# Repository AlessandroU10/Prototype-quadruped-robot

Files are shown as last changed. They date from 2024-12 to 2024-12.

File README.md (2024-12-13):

# Quadruped Robot Prototype

Este proyecto presenta el diseño de un prototipo de robot cuadrúpedo, enfocándose en el cálculo de torques, análisis cinemáticos y validación experimental.
Cálculo de Torques: Se consideran torques estáticos (fuerzas aplicadas y momentos de inercia) y dinámicos (aceleraciones angulares y fuerzas inerciales).
Cinemática Directa e Inversa: Determinación de la posición y orientación del efector final mediante transformadas homogéneas y cálculo de configuraciones articulares para alcanzar objetivos específicos.
Cinemática Diferencial: Uso del Jacobiano analítico para relacionar velocidades articulares y lineales, identificando singularidades que afectan el sistema.
Validación: Verificación de la cinemática directa con herramientas CAD y simulación.

## Keywords
Diseño Mecánico, Robot cuadrúpedo, Cinemáticadirecta, Cinemática Inversa. 

## Authors
- Alesandro Paredes Zenteno
- Luis Alfredo Villafani Sandoval
- Adrian Urriolagotia Marino

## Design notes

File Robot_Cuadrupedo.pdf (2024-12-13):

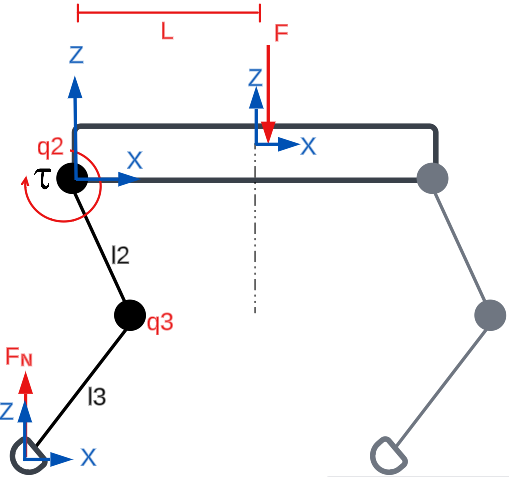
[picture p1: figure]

Departamento de Ingeniería Mecatrónica Robótica (IMT-342) / Número de información 001 @ 2024 Universidad Católica Boliviana "San Pablo" – Unidad Santa Cruz

# Diseño de prototipo de Robot Cuadrúpedo

Resumen: El documento aborda el diseño de un prototipo de robot cuadrúpedo enfatizando aspectos como el cálculo de torques, análisis cinemáticos y verificación experimental. En el dimensionamiento de motores, se analizan tanto el torque estático, basado en fuerzas aplicadas y momentos de inercia, como el torque dinámico, que incorpora aceleraciones angulares y fuerzas inerciales. El análisis de cinemática directa permite determinar la posición y orientación del efector final a través de transformadas homogéneas, mientras que la cinemática inversa calcula las configuraciones articulares necesarias para alcanzar una posición objetivo. La cinemática diferencial, mediante el Jacobiano analítico, relaciona velocidades articulares y lineales, permitiendo detectar singularidades que afectan el rendimiento del sistema. Finalmente, la cinemática directa se verifica empleando herramientas CAD y software de simulación, verificando el modelo planteado.

Palabras clave: Diseño Mecánico, Robot cuadrúpedo, Cinemática directa, Cinemática Inversa.

I.INTRODUCCIÓN
El diseño y desarrollo de robots cuadrúpedos ha capturado la atención de la comunidad científica debido a su capacidad para adaptarse a diversos terrenos y emular características biomecánicas de animales [1]. Entre los desafíos más relevantes para este diseño, se destaca el cálculo de torques para los motores, así como la implementación de análisis cinemático directa, inversa y diferenciales para lograr movimientos de cada extremidad del robot. El objetivo de este proyecto es verificar la cinemática directa e inversa de un prototipo de robot cuadrúpedo mediante simulaciones y pruebas experimentales.

El diseño de torques en robots cuadrúpedos, tanto estáticos como dinámicos, requiere una comprensión detallada de las fuerzas involucradas y de los momentos de inercia de los sistemas rotacionales. Estos cálculos no solo garantizan la estabilidad durante el desplazamiento, sino que también optimizan el consumo energético del robot [2].

Por otra parte, el análisis de la cinemateca directa se centra en determinar la posición y orientación del efector final con base en las variables articulares, mientras que la cinemática inversa busca resolver las configuraciones necesarias de los motores para alcanzar una posición deseada [3]. La cinemática diferencial, por su parte, facilita el análisis de velocidades y fuerzas en tiempo real, siendo una herramienta esencial para controlar la interacción del robot con su entorno

En este contexto, el método de transformadas homogéneas ha demostrado ser eficaz para analizar movimientos de sistemas complejos, como extremidades de robots cuadrúpedos [4]. Además, el uso del Jacobiano analítico permite identificar configuraciones críticas, como puntos de singularidad, que limitan los grados de libertad y afectan el rendimiento general del robot [5].

Por lo tanto, este documento se enfoca en el desarrollo de un prototipo de robot cuadrúpedo que integre estos conceptos, utilizando herramientas de simulación y verificación experimental para garantizar su funcionalidad.

II. DISEÑO DEL ROBOT CUADRÚPEDO

A. Calculo de torque
a) Estatico
El torque estático se calcula en base a la Ec.1.
τest = FL | (1)

Donde:

F | Fuerza aplicada al cuerpo del robot
L | Distancia del centro de masa al eje de rotación

No obstante, debido a la fuerza aplicada (se incluye la masa de una extremidad) en la base del robot, existe una fuerza normal opuesta a la dirección de la fuerza aplicada como se muestra en la Fig.1.

Fig. 1 Diagrama cinemático en vista lateral [Elaboración Propia]

Según la segunda ley de Newton ∑ FZ = ma, se determina la fuerza normal en base a la Ec.2.
FN = F | (2)

Adrian Urriolagotia Marino Dept. Ing. Mecatrónica
Universidad Católica Boliviana Santa Cruz de la Sierra, Bolivia adrian.uriolagotia@ucb.edu.bo

Luis Alfredo Villafani Sandoval Dept. Ing. Mecatrónica
Universidad Católica Boliviana Santa Cruz de la Sierra, Bolivia luis.villafani@ucb.edu.bo

Alesandro Paredes Zenteno
Dept. Ing. Mecatrónica
Universidad Católica Boliviana Santa Cruz de la Sierra, Bolivia alesandro.paredes@ucb.edu.bo

Mgs. José Jesús Cabrera
Dept. Ing. Mecatrónica
Universidad Católica Boliviana Santa Cruz de la Sierra, Bolivia jcabrera@ucb.edu.bo

Departamento de Ingeniería Mecatrónica Robótica (IMT-342) / Número de información 001 @ 2024

Cuando el cuerpo del robot permanece en reposo, la aceleración resulta nula. Esta condición implica que el sistema se encuentra en equilibrio, donde la fuerza normal contrarresta exactamente la fuerza aplicada. En conclusión, la ausencia de aceleración garantiza el balance de fuerzas en el cuerpo.

Considerando lo anterior, en la Tabla 1 se presenta los valores para determinar el torque estático para el motor q2 de una extremidad del robot cuadrúpedo.
TABLA 1 DATOS DE DISEÑO [Elaboración Propia]
N.º | DATOS DEL DISEÑO
Datos | Valor | Unidad
1 | Longitud (L) | 0,07 | m
2 | Masa de carga / 4 | 0,25 | kg
3 | Fuerza (F) | 2,5 | N

De acuerdo a los datos de la Tabla 1, se calcula el torque estático en base a la Ec.1, resultando τest = 0,175 Nm.

b) Dinamico
El torque dinámico corresponde al momento de fuerza necesario para mover un sistema rotacional sujeto a aceleración. Este concepto incluye la resistencia inercial del sistema y las fuerzas externas aplicadas durante el movimiento. La ecuación que describe el torque dinámico se presenta en la Ec.3.
τdin = Imq̈2 + ILq̈2 + τf + τi
(3)

Donde:

Im | Momento de inercia del motor
q̈2 | Aceleración angular
IL | Momento de inercia de la carga
τf | Torque de fricción
τl | Torque de fuerza inercial

En base a la Fig. 1, el motor q2
recibe el mayor torque, debido a que se encuentra a la máxima distancia L desde el eje del motor hasta el centro de masa del robot y conlleva el peso de toda la extremidad para un desplazamiento lineal.

En la Tabla 2 se presentan los datos de diseño.
TABLA 2 DATOS DE DISEÑO [Elaboración Propia]
N.º | DATOS DEL DISEÑO
Datos | Valor | Unidad
1 | Longitud (L) | 0,07 | m
2 | Masa (l2) | 0,015 | kg
3 | Masa (l3) | 0,01 | kg
4 | Masa de carga / 4 | 0,25 | kg
5 | Masa servo motor estimada | 0,015 | kg

La masa total de una extremidad del robot cuadrúpedo se expresa en la Ec.5.
mt = ml2 + ml3 + mq2 + mL
mt = 0.3[Kg] | (5)

El momento de inercia de la carga se presenta en la Ec.6.

IL =

1
3

mLL

2 | (6)

En base a la Ec.6, el momento de inercia de la carga resulta IL = 5x10⁻⁴

[kgm²
].

Según [6], el momento de inercia de un servo motor DC, está dado por Ec.7.
Im = 1,4x10⁻⁶

[Kgm²
] | (7)

Se considera un torque de fricción τf para el cálculo de torque dinámico del motor, según [6], el torque de fricción τf se representa como la Ec.8.
τf = Bmq̇2

(8)

Donde:

τf | Torque de fricción
Bm | Constante de fricción viscosa
q̇2 | Velocidad angula del motor

Para calcular Bm se utiliza la ecuación de la constante de tiempo mecánica del sistema dada por la Ec.9.

Bm =

Im
tm

−

kbkm
Rm

(9)

Donde:

Im | Momento de inercia del motor
tm | Constante de tiempo mecánica
kb, km | Constantes de fuerza electromotriz y de torque
Rm | Resistencia del motor

Según [6], las características del fabricante de un motor DC se presentan en la Tabla 3.

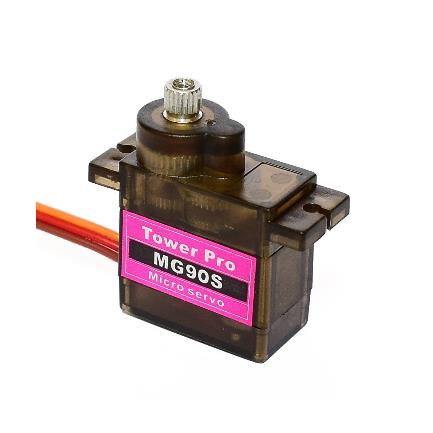
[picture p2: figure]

Departamento de Ingeniería Mecatrónica Robótica (IMT-342) / Número de información 001 @ 2024

TABLA 3 CARACTERISTICAS DEL MOTOR [6]

Nº | MOTOR DC
PARAMETRO | VALOR | UNIDADES

1

2

3

4

5

Dado los valores en la Tabla 6, la constante de fricción viscosa en base a la Ec.9, resulta Bm = 2,012x10⁻⁶Nms.

Los requerimientos del motor se presentan en la Tabla 4.

TABLA 4 REQUERIMIENTOS DEL MOTOR [Elaboración Propia]

Nº | REQUERIMIENTOS DEL MOTOR
REQUERIMIENTO | VALOR | UNIDAD
1 | | 1,4x10⁻⁶ | Kgm²
2 | | 5x10⁻⁴ | Kgm²
3 | q̇2
4 | q̈2

Considerando el requerimiento de q̇2 de la Tabla 4, se calcula el torque de fricción en base a la Ec.8, resultando τf = 1,6x10⁻⁵Nm

La aceleración lineal se considera en el cálculo de torque dinámico debido a que la masa de la extremidad experimenta un movimiento lineal relacionado con la rotación. Esto ocurre porque una aceleración lineal en una masa genera fuerzas inerciales que contribuyen al torque dinámico.

La aceleración lineal se presenta en la Ec.10. dando como resultado: a = 0,35 m
s

2
a = q̈2L | (10)

La ecuación de la fuerza inercial en el centro de masa se presenta en la Ec.11, resultando Finer = 8,75x10⁻³N

Finer = mpataa | (11)

El torque inercial debido a esta fuerza se presenta en la Ec.12, dando como resultado τiner = 6,125x10⁻⁴Nm

τiner = FinerL | (12)

En base a la Ec.3, se obtiene el cálculo del torque dinámico para el motor q2

, que corresponde a: τdin = 3,14x10⁻³Nm.

B. Dimensionamiento de motor
El torque máximo del motor q2
se presenta en la Ec.13,
dando como resultado τmax = 0,18 Nm.
τmax = τesta + τdin | (13)

Según este valor de referencia se dimensiona el servo motor a implementar para una entremediad del robot cuadrúpedo.

Fig. 2 Servo motor MG90S [7]

El servomotor MG90S, mostrado en la Fig. 2, cumple con el torque requerido para el prototipo del robot cuadrúpedo. Las especificaciones técnicas de este servomotor se encuentran detalladas en la Tabla 5. Por lo tanto, este modelo resulta adecuado para las necesidades del proyecto.

TABLA 5 ESPECIFICACIONES DEL MOTOR [7]

Nº | REQUERIMIENTOS DEL MOTOR
REQUERIMIENTO | VALOR | UNIDAD
1 | Voltaje de operación | 3 – 7,2 | VDC
2 | Torque | 0,2 | Nm
3 | Velocidad | 0,1 / 60 | seg grados ⁄
4 | Ancho de pulso | 600 y 240 | μs
5 | Engranajes | Metal
6 | Dimensiones | 22 x 11,5 x 27 | mm
7 | Peso | 13,4 | g

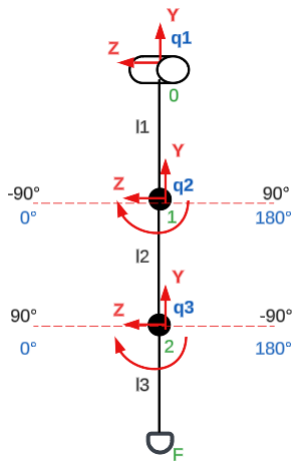
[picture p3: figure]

Departamento de Ingeniería Mecatrónica Robótica (IMT-342) / Número de información 001 @ 2024

C. Selección de componentes
La Tabla 6 se presentan los componentes a utilizar para el desarrollo del robot cuadrúpedo.
TABLA 6 SELECCIÓN DE COMPONENTES [Elaboración Propia]
Nº | Selección de Componentes
Categoría | Componente/ Pieza | Cantidad
1 | Componentes | Arduino uno | 1
2 | | Servo motor MG90S | 6
3 | Elementos Impresos/Externos | Corona | 6
4 | | Base | 1
5 | | Fémur | 2
6 | | Tibia | 2
7 | | Pata de goma | 2
8 | | Pieza 1 izquierda | 1
9 | | Pieza 2 izquierda | 1
10 | | Pieza 1 derecha | 1

Soportes para
Motor
11 | Pieza 2 derecha | 1
III. | ANÁLISIS CINEMÁTICO
A. Cinematica Directa
En la Fig.3 se presenta el diagrama cinemático de una extremidad del robot cuadrúpedo. Se observa que los motores q2 y q3 giran físicamente de 0º a 180º en sentido horario, sin embargo, en la cinemática directa los ángulos se establecen de 90º a -90º grados sentido antihorario siendo 0º en una posición vertical.

Fig. 3 Diagrama cinemático [Elaboracion propia]

Se utiliza el método de transformadas homogéneas para determinar la posición y orientación del punto final, de ese modo obtener la cinemática directa de una extremidad. El análisis se realiza en base a la Fig.3 en un plano Y-Z donde se obtiene las transformada de TI0

, T01, T12 y T2F.

Para simplificar la expresión matemática se considera la notación presentada en la Ec.14 a la Ec.19.

C23 = cos (q

2

− q
3

)
(14)

S23 = sin (q

2

− q
3

)
(15)

C1 = cos(q1)

(16)

S1 = sin(q1)

(17)

C2 = cos(q2)

(18)

S2 = sin(q2)

(19)

En la Ec.20 se presenta la transformada homogénea desde el sistema de coordenadas inercial I al punto 0 donde solo existe una rotación en Z.
TI0 = [
C1 | −S1 | 0
S1 | C1 | 0
0
0 | 0
| 0 | 1
| | 0

0
0

0/1]

(20)

En la Ec.21 se presenta la trasformada homogénea de 0 a 1, donde existe translación en Y y rotación en X.
T01 = [
1 | 0 | 0
0 C2 | −S2
0
0 | S2
| 0 | S2
| | 0

a
−l1
b
1

]

(21)

En la Ec.22 se presenta la trasformada homogénea de 1 a 2, donde existe traslación en Y y rotación en X.
T12 = [
1 | 0 | 0
0 C3 | −S3
0
0 | S3
| 0 | S3
| | 0

c
−l2

0/1]

(22)

Finalmente, en la Ec.23 se presenta la trasformada homogénea de 2 a F, donde solo existe una traslación en Y.

T2F = [

1 0 0
0 1 0
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
(23)

En la Tabla 7 se presenta el valor de las translaciones y desfases que contiene una extremidad.

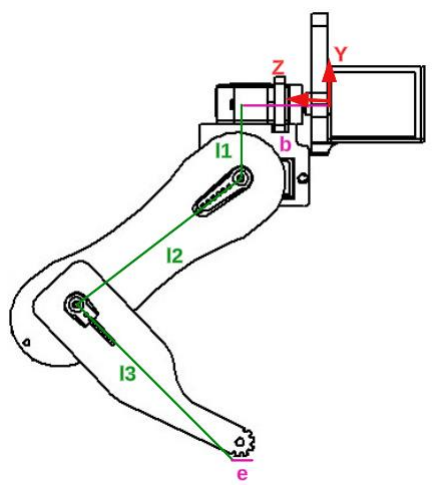
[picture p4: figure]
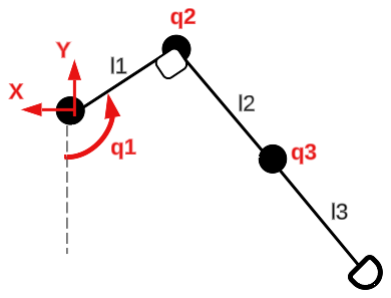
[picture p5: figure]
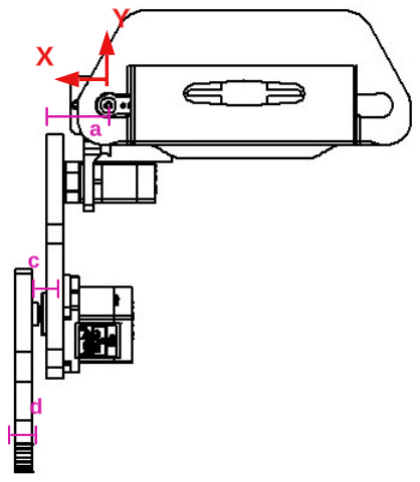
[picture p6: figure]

Departamento de Ingeniería Mecatrónica Robótica (IMT-342) / Número de información 001 @ 2024

TABLA 7 VALOR DE TRANSLACIONES Y DESFASES [Elaboración Propia]

Nº | DATOS DE DIAGRAMA CINEMÁTICO
LONGITUD | VALOR | UNIDAD
1 | a | 17,66 | mm
2 | b | 24,25 | mm
3 | c | 6,9 | mm
4 | d | 0,5 | mm
5 | e | 7,96 | mm
6 | l1 | 22,93 | mm
7 | l2 | 64,49 | mm
8 | l3 | 70,54 | mm

En la Fig.4 y Fig. 5 se observa la ubicación de dichas variables las cuales representan el desfaz que existe entre cada motor y eslabón de una extremidad.

Fig.4 Plano Y-Z de una extremidad [Elaboracion propia]

Fig.5 Plano Y-X de una extremidad [Elaboracion propia]

La transformada homogénea desde el sistema de coordenadas inercial I hasta el punto final F se define como el producto de todas las transformadas intermedias como se presenta el Ec.24.

TIF = TI0T01T12T2F

(24)

De la Ec.24 se obtiene la matriz presentada en la Ec.25 donde se muestra la orientación y posición del punto final.

TIF = [

C1 | −S1C23 | S1S23
S1 | C1C23 | −S23C1
0
0 | S23
| 0 | C23
| | 0

PX
PY
PZ
1

]
(25)

Donde:
Px = aC1 + cC1 + dC1 + eS1S23 + l1S1 + l2S1C2 + l3S1C23 Py = aS1 + cS1 + dS1 − eS23C1 − l1C1 − l2C1C2 − l3C1C23

Pz = b + eC23 − l2S2 − l3S23

La transformada homogénea para las articulaciones restantes presenta una estructura equivalente debido a la similitud en su naturaleza. En conclusión, dicha uniformidad simplifica el análisis y generaliza el procedimiento aplicado.

B. Cinematica Inversa
Mediante el método cerrado, se determina la cinemateca inversa para los motores q1

, q2

, q3
. La Fig.6 presenta el
diagrama cinemático para q1 donde se obtiene la Ec.26. en base a [9].

q1 = tan⁻¹ (

x − c − d
y + l1

) + cos⁻¹ (
a
√(x − c − d)
2 + (y + l1)

2

) (26)

Fig.6 Diagrama cinemático en el plano Y-X [Elaboracion propia]

En la Fig.7 se presenta el diagrama cinemático en el plano Y-Z para q2 y q3 donde se obtiene geométricamente la Ec.27 y Ec.28.

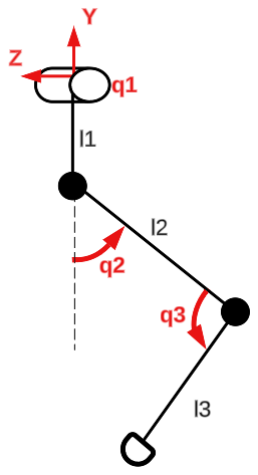
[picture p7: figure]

Departamento de Ingeniería Mecatrónica Robótica (IMT-342) / Número de información 001 @ 2024

Fig.7 Diagrama cinemático en el plano Y-Z [Elaboracion propia]

q2 =

π
2

+ sin⁻¹ (

z + b
√L − a
2

) − cos⁻¹ (
b

2 − a

2 − c

2
2b√L − a
2

) (27)

q3 = cos⁻¹ (
a

2 + b

2 + c

2 − L
2bc | ) | (28)

Donde:
L = (x − c − d)

2 + (z − b)

2 + (y + l1
)

2

C. Cinematica Diferencial
a) Jacobiano Analítico
El Jacobiano Analítico relaciona las velocidades de los motores q̇1

, q̇2 y q̇3 con la velocidad lineal del efector final y viene dada por la Ec.29.

V = J ∗ q̇

(29)

Se determina las derivadas parciales de Px, Py, Pz respecto a
cada articulación q1

, q2

, q3 en base a la Ec.30.

TBF =

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
∂q3 ]

(30)

Donde:

Respecto a q1

∂x
∂q1

= −aS1 − cS1 − dS1 + eS23C1 + l1C1 + l2C1C2 + l3C1C23

∂y
∂q1

= aC1 + cC1 + dC1 + eS1S23 + l1S1 + l2S1C2 + l3S1C23

∂z
∂q1

= 0

Respecto a q2
:
∂x
∂q2

= (eC23 − l2S2 − l3S23)S1

∂y
∂q2

= (−eC23 + l2S2 + l3S23)C1

∂z
∂q2

= −eS23 − l2C2 − l3C23

Respecto a q3
:
∂x
∂q3

= (−eC23 + l3S23)S1

∂y
∂q3

= (eC23 − l3S23)C1

∂z
∂q3

= eS23 + l3C23

b) Singularidad
La singularidad se establece mediante la determinante de la Jacobiano, esta condición indica configuraciones específicas donde la extremidad pierde grados de libertad, afectando su capacidad de movimiento en ciertas direcciones.

El determinante de la matriz Jacobiana se presenta en la Ec.31.

det(JA

) = l2(e

2S23C3 + el1C3 + el2C2C3 + el3S3S23 + el3C3C23 + l1l3S3 + l2l3S3C2 + l3

2
S3C23)

(31)

Se | identificaron | condiciones | que | conducen | a
configuraciones singulares las cuales son:
q2 = q3 = 0°
q2 = 90°, q3 = 0°
q2 = −90°, q3 = 0°

IV. ESPACIO DE TRABAJO
a) Simualcion
En laFig.8 se presenta la simulación del espacio de trabajo de una extremidad simulado en Matlab en base a la cinemateca directa utilizando los rangos de trabajo de la Tabla 8.

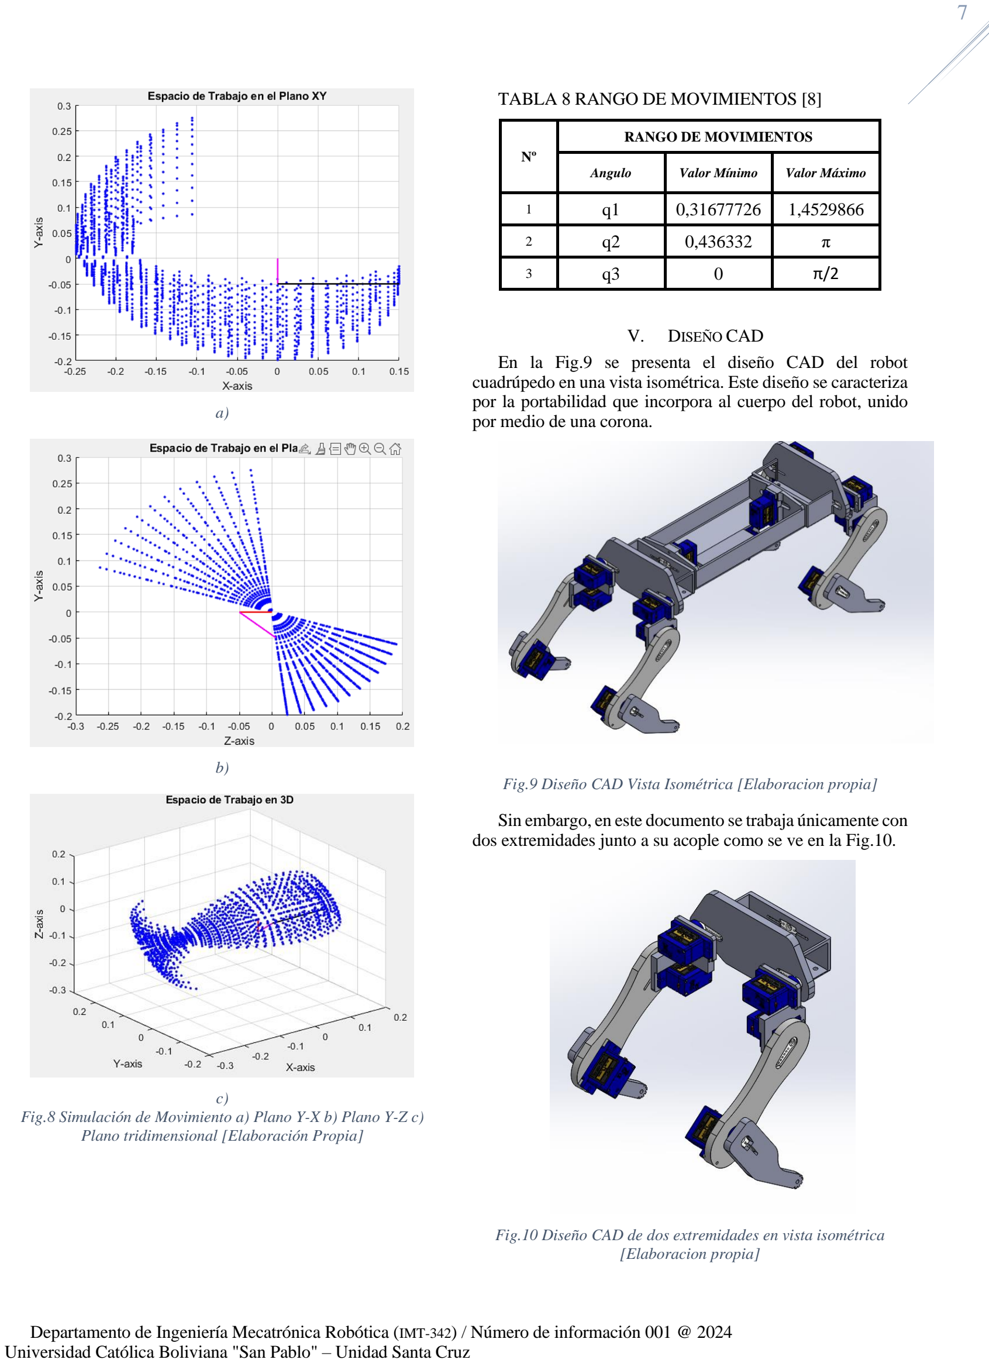
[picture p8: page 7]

Departamento de Ingeniería Mecatrónica Robótica (IMT-342) / Número de información 001 @ 2024

a)

b)

c)
Fig.8 Simulación de Movimiento a) Plano Y-X b) Plano Y-Z c) Plano tridimensional [Elaboración Propia]

TABLA 8 RANGO DE MOVIMIENTOS [8]

Nº | RANGO DE MOVIMIENTOS
Angulo | Valor Mínimo | Valor Máximo
1 | q1 | 0,31677726 | 1,4529866
2 | q2 | 0,436332 | π
3 | q3 | 0 | π/2
V. DISEÑO CAD
En la Fig.9 se presenta el diseño CAD del robot cuadrúpedo en una vista isométrica. Este diseño se caracteriza por la portabilidad que incorpora al cuerpo del robot, unido por medio de una corona.

Fig.9 Diseño CAD Vista Isométrica [Elaboracion propia]

Sin embargo, en este documento se trabaja únicamente con dos extremidades junto a su acople como se ve en la Fig.10.

Fig.10 Diseño CAD de dos extremidades en vista isométrica [Elaboracion propia]

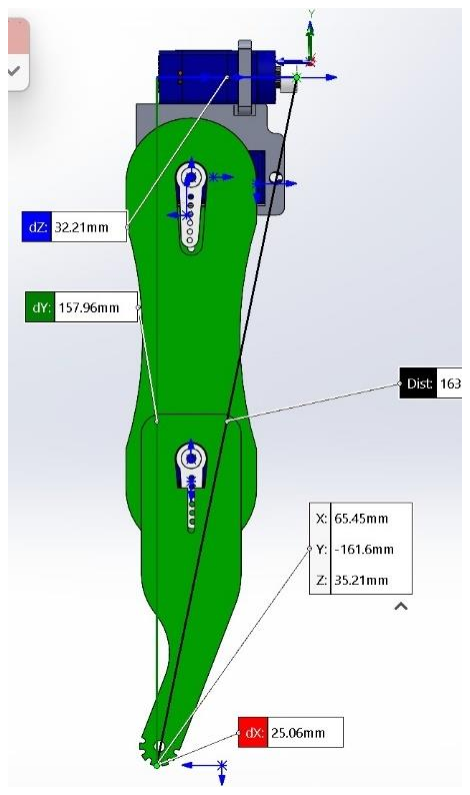
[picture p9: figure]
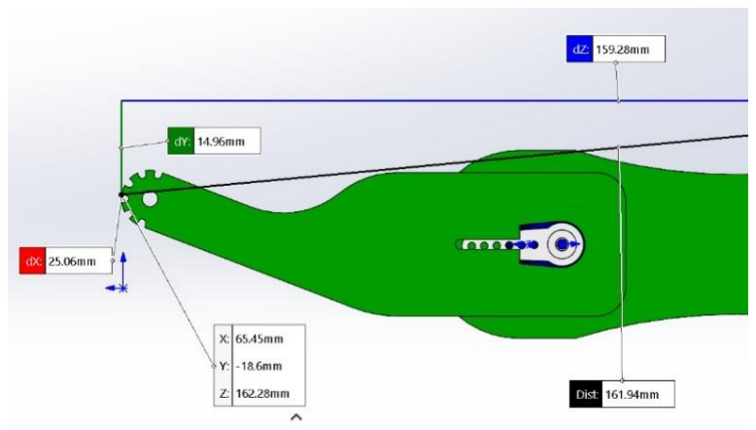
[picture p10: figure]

Departamento de Ingeniería Mecatrónica Robótica (IMT-342) / Número de información 001 @ 2024

VI. VERIFICACIÓN

A. Comprobacion de cinematica directa
Para la comprobación de la cinemática directa se calcula la posición del efector final mediante software VS CODE y se comprueba dicha posición en el software de diseño CAD SOLIDWORKS.

Se presentan tres casos de estudio en cuanto a las posiciones de q2 y q3

siendo q1 = 0°, las cuales se presentan en la Tabla 9.

TABLA 9 CASOS DE ESTUDIO [Elaboración Propia]

Caso | RANGO DE MOVIMIENTOS EN GRADOS °
Motor | Valor
1 | q2 | 0°
| q3 | 0°
2 | q2 | -90°
| q3 | 0°
3 | q2 | 90°
| q3 | 90°
a) Caso 1
Para el caso 1 se presenta la extremidad con un ángulo de q2 = q3 = 0°, resultando la posición final en:

X = [
Px
Py
Pz

] = [
25,06
−157,96

32,21 ]

En la Fig.10 se presenta la extremidad modelada en CAD, donde se determina la distancia en los ejes desde el sistema de coordenadas inercial hasta el punto final. Las mediciones realizadas en x, y, z coinciden con los valores obtenidos en Px, Py, Pz
. Este resultado verifica la comprobación de la cinemateca directa.

Fig. 10 Extremidad con q2

= q3

= 0° [Elaboracion propia]

b) Caso 2
Se comprueba la cinemática directa para q2 = −90° y q3 = 0° , resultando la posición final en:

X = [
Px
Py
Pz

] = [
25,06
−14,97

159,28]

En la Fig.11 se presenta la extremosidad en cuyos ángulos establecidos, donde se observa que las dimensiones en x, y, z corresponden a Px, Py, Pz
(Se recorto la Fig.11 por tema de visualización).

Fig.11 Extremidad con q2

= −90° y q3

= 0°[Elaboracion
propia]

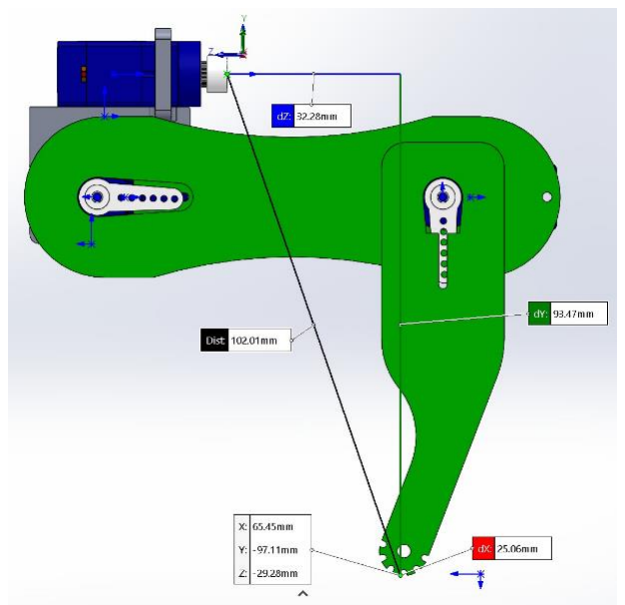
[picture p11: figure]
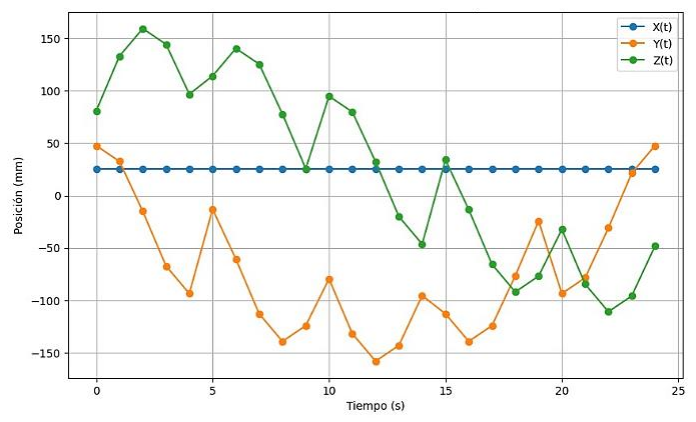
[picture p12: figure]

Departamento de Ingeniería Mecatrónica Robótica (IMT-342) / Número de información 001 @ 2024

c) Caso 3
Se presenta la Fig. 12 para q2 = 90° y q3 = 90° , resultado la cinemateca directa en:
X = [
Px
Py
Pz

] = [
25,06
−93,47

−32,28]

Fig.12 Extremidad con q2

= q3

= 90° [Elaboracion propia]

En la Fig.12 se observa que las dimensiones en x, y, z, corresponden a Px, Py, Pz

La cinemática directa de una extremidad se planteó correctamente, como se verifico al comparar Px, Py, Pz con x, y, z, obtenidas del diseño CAD en los tres casos de estudio.

VII. SIMULACIÓN
Se realiza la simulación en tiempo real de la cinemática directa en Matlab con los siguientes ángulos (q1
, q2

, q3

)
presentados en la Tabla 10.

TABLA 10 RANGO DE MOVIMIENTOS [Elaboración Propia]

Nº | RANGO DE MOVIMIENTO EN GRADOS °
q1 | q2 | q3
1 | 0 | -90 | 90
2 | 0 | -90 | 45
3 | 0 | -90 | 0
4 | 0 | -90 | 45
5 | 0 | -90 | 90
6 | 0 | -45 | 90
7 | 0 | 0 | 90
8 | 0 | 0 | 45
9 | 0 | 0 | 0
10 | 0 | 0 | -45
11 | 0 | 0 | -90
12 | 0 | 45 | -45
13 | 0 | 90 | 0
14 | 0 | 90 | 45
15 | 0 | 90 | 90
16 | 0 | 90 | 45
17 | 0 | 90 | 0
18 | 0 | 90 | 45
19 | 0 | 90 | -90

La Fig.13 presenta el comportamiento de las posiciones x, y, z del punto final a lo largo del tiempo.

Fig.13 Grafica de posición final vs tiempo [Elaboracion propia]

La curva x(t)

se mantiene constante debido a que q1 se
encuentra en 0

°
lo cual corresponde a la inclinación de la pata. La curva y(t) muestra oscilaciones con amplitudes positivas y negativas, atribuibles a las rotaciones de los eslabones. Por otra parte, la curva z(t) presenta oscilaciones menos pronunciadas, lo que sugiere un efecto más moderado de las rotaciones sobre este eje en la posición del punto final.

VIII. EXPERIMENTOS
Se realiza pruebas experimentales para la validación de la cinemática directa mediante Arduino. Se programó los motores q1

, q2

, q3 para graficar la posición del punto final en tiempo real. En la Fig.14 se presenta el comportamiento de la posición x, y, z del punto final, mientras que en la Fig.15 se
observa | la | pata/extremidad | aplicando | la | respectiva
modelación.

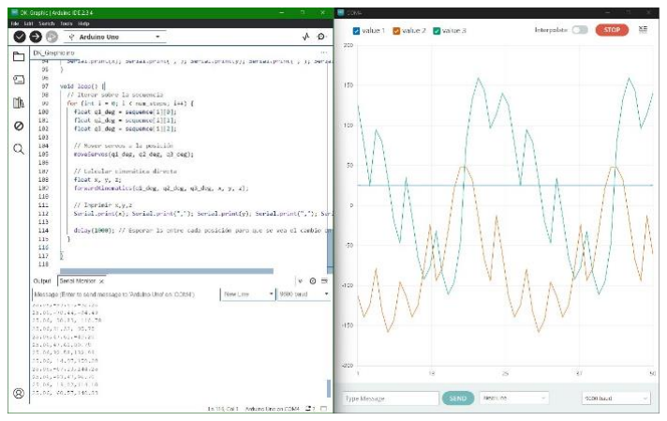
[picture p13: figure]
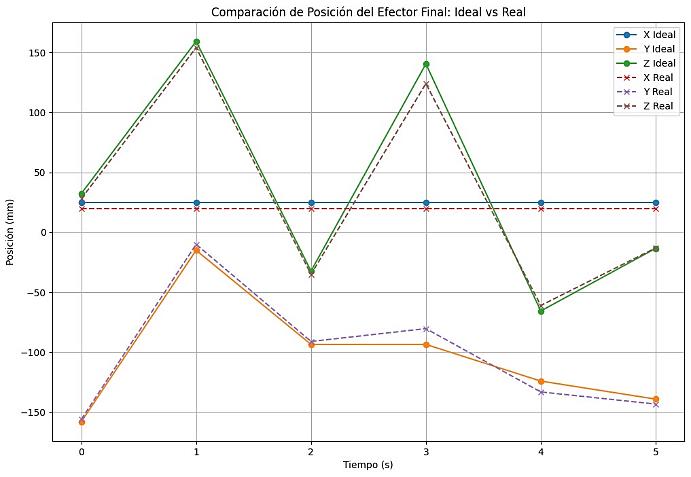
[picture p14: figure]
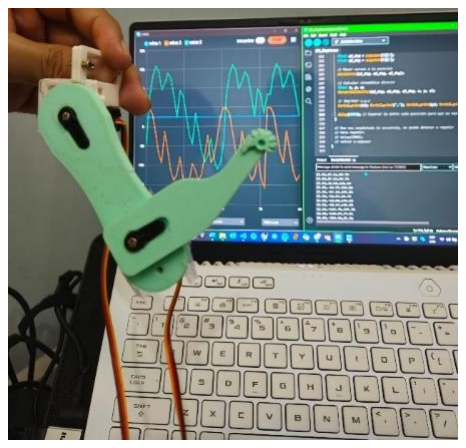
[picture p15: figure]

Departamento de Ingeniería Mecatrónica Robótica (IMT-342) / Número de información 001 @ 2024

Fig. 14 Comportamiento de x, y, z en tiempo real [Elaboracion propia]

Fig.15 Aplicación de la DK en una extremidad [Elaboracion propia]

Seguidamente se realiza seis pruebas experimentales para valores de q1

, q2

, q3 presentadas en la Tabla 11. Esto con el fin de conocer si la posición ideal del punto final es igual a la posición final experimental.

TABLA 11 VALORES IDEAL Y REALES [Elaboración Propia]

Caso | DATOS DE POSICION FINAL
X Ideal | X Real | Y Ideal | Y Real | Z Ideal | Z Real
1 | 25,06 | 20 | -157,96 | -156 | 32,21 | 28
2 | 25,06 | 20 | -14,97 | -10 | 159,28 | 154
3 | 25,06 | 20 | -93,47 | -91 | -32,28 | -35
4 | 25,06 | 20 | -93,47 | -80,3 | 140,39 | 124
5 | 25,06 | 20 | -124,03 | -133,1 | -65,60 | -61
6 | 25,06 | 20 | -139,07 | -143,2 | -13,39 | -13

En la Fig.16 se observa la gráfica de ambas posiciones tanto ideal como experimental para los seis casos de estudio, dada esta comparación existe una diferencia denominada error en relación a la posición del punto final dada por la Ec.32, los cuales se presentan en la Tabla 12.
e = ideal − real | (32)

Donde:

e : error

ideal : valor ideal de la posición final

real : valor real/experimental de la posición final

Fig.16 Comparación de valor ideal con el valor real de la posición final [Elaboracion propia]

TABLA 12 ERROR EN % [Elaboración Propia]

Caso | ERROR EN %
X | Y | Z
1 | 20,19 | 1,24 | 13,07
2 | 20,19 | 33,2 | 3,31
3 | 20,19 | 2,64 | 8,42
4 | 20,19 | 14,09 | 11,67
5 | 20,19 | 7,31 | 7,01
6 | 20,19 | 2,96 | 2,91
IX. | CONCLUSIÓN
El diseño del prototipo de robot cuadrúpedo permitió cumplir con el objetivo planteado de verificar la cinemática directa, mediante simulaciones como experimentalmente.

A través del análisis de torque estático y dinámico, se logró dimensionar los motores que cumplan con el peso/fuerza aplicada al robot. El método de transformadas homogéneas y método cerrado facilitaron el análisis y la obtención de la cinemática directa e inversa.

Las simulaciones realizadas en MATLAB y el diseño CAD en SolidWorks confirmaron la validez del cálculo de la cinemática directa, mientras que las pruebas experimentales con Arduino corroboraron la correspondencia con los valores ideales, de ese modo se obtuvo un error sobre el valor ideal y experimental del punto final el cual no sobrepasa del 15% para cada caso. Por tanto, este proyecto sienta las bases para futuros desarrollos en robótica, contribuyendo al avance en el diseño de robots cuadrúpedos o aplicaciones semejantes.

Departamento de Ingeniería Mecatrónica Robótica (IMT-342) / Número de información 001 @ 2024

X. BIBLIOGRAFIA
[1] Y. Li, B. Li, J. Ruan, and X. Rong, “Research of mammal bionic quadruped robots: A review,” in 2011 IEEE 5th International Conference on Robotics, Automation and Mechatronics (RAM), IEEE, Sep. 2011, pp. 166–171. doi: 10.1109/RAMECH.2011.6070476.
[2] P. Gonzalez de Santos, M. A. Jimenez, and M. A. Armada, “Dynamic Effects in Statically Stable Walking Machines,” J Intell Robot Syst, vol. 23, no. 1, pp. 71–85, 1998, doi: 10.1023/A:1007993923530.
[3] K. Harada, S. Russo, T. Ranzani, A. Menciassi, and
P. Dario, “Design of Scout Robot as a robotic module for symbiotic multi-robot organisms,” in 2011 International Symposium on Micro-NanoMechatronics and Human
Science, | IEEE, | Nov. | 2011, | pp. | 511–513. | doi:
10.1109/MHS.2011.6102244.
[4] P. G. De Santos, E. Garcia, and J. Estremera, Quadrupedal locomotion: an introduction to the control of four-legged robots, vol. 1. Springer, 2006.
[5] Y. Fukuoka and H. Kimura, “Dynamic Locomotion of a Biomorphic Quadruped ‘ Tekken ’ Robot Using Various Gaits: Walk, Trot, Free‐Gait and Bound,” Appl Bionics Biomech, vol. 6, no. 1, pp. 63–71, Jan. 2009, doi: 10.1080/11762320902734208.
[6] F. M.-H. &. A. &. B. Larraga, «Modelado de un motor DC,» 2024.
[7] NAYLAMP. | [En | línea]. | Available:
https://naylampmechatronics.com/servomotores/246-micro-servo-mg90s.html (https://naylampmechatronics.com/servomotores/246-micro-servo-mg90s.html)
[8] L. A. B. &. B. R. R. M. &. A. A. Diaz, «Diseño de Prototipo de Micro Robot Cuadrúpedo,» 2023

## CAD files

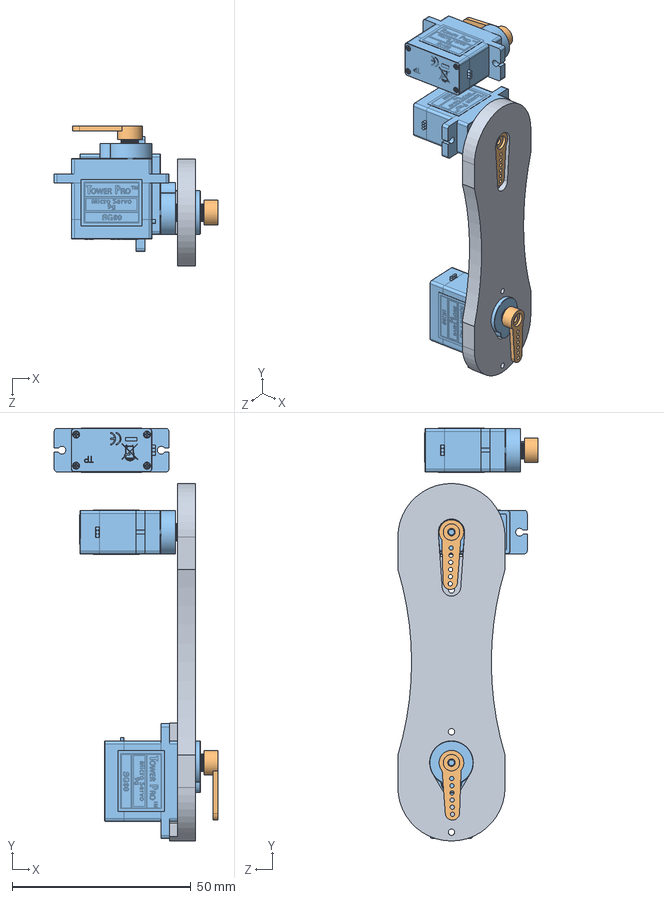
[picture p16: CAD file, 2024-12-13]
CAD/BackLeg_CAD/LegBack.SLDASM
45.8 x 115.5 x 39.2 mm
SG90 - Micro Servo 9g - Tower Pro.1 x 3
SG90 - Micro Servo 9g - Tower Pro.2 x 3
Fermur_robot_V3

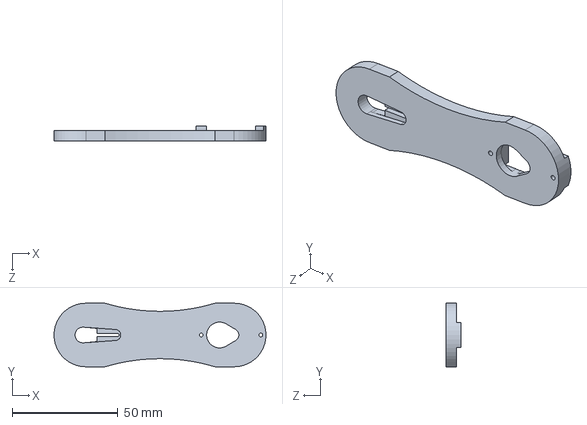
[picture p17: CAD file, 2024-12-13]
CAD/BackLeg_CAD/Fermur_robot_V3.SLDPRT
100.0 x 30.0 x 7.15 mm

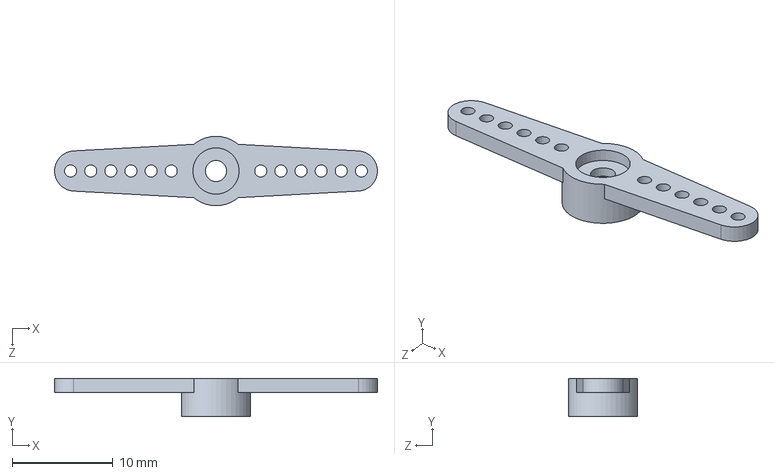
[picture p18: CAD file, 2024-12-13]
CAD/BodyComplete_CAD/SG90 - Micro Servo 9g - Tower Pro.3.SLDPRT
32.1 x 3.80 x 6.90 mm

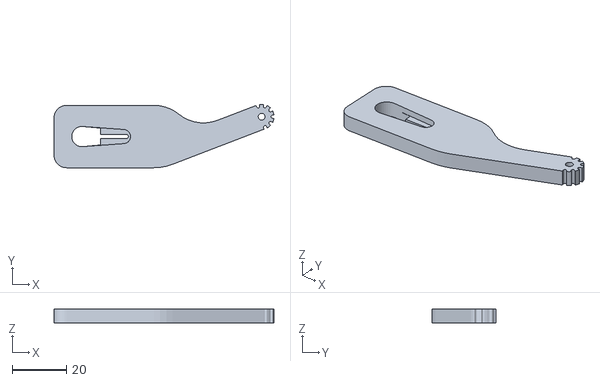
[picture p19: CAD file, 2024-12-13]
CAD/STL_Files/Fermur_pata_V3.STL
80.8 x 23.3 x 5.00

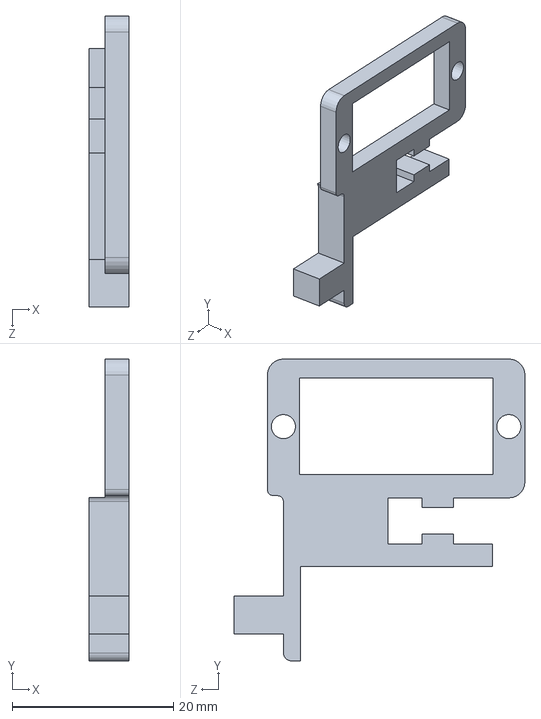
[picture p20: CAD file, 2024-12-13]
CAD/BackLeg_CAD/Piece2R.SLDPRT
5.00 x 37.5 x 36.1 mm

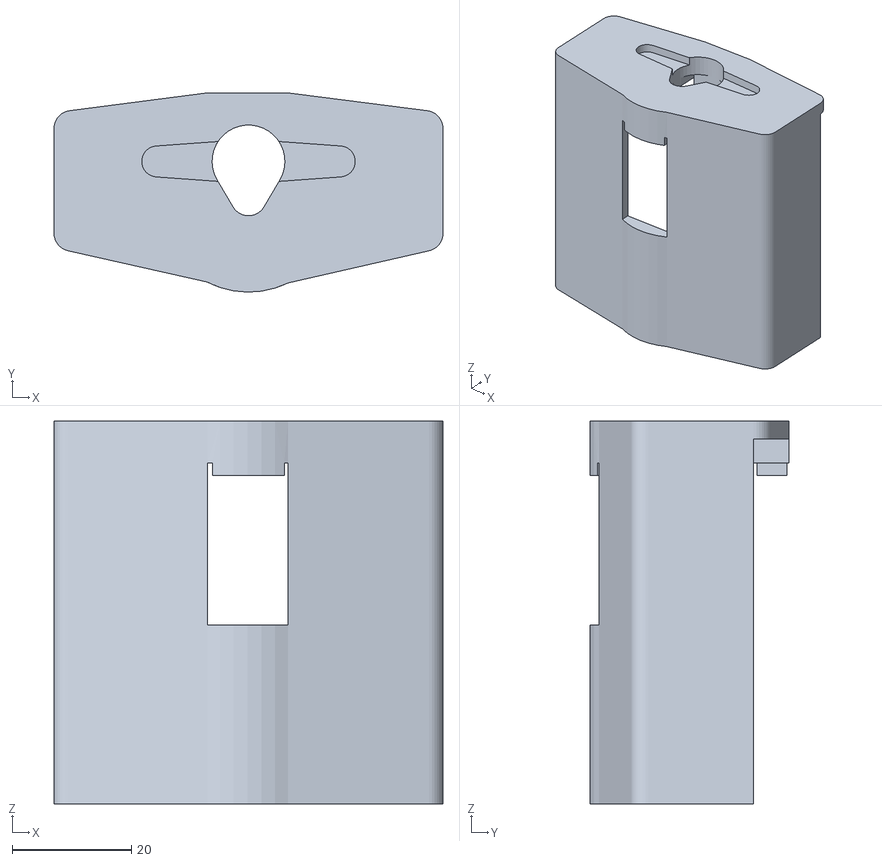
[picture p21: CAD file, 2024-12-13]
CAD/STL_Files/Body.STL
65.2 x 33.4 x 64.2

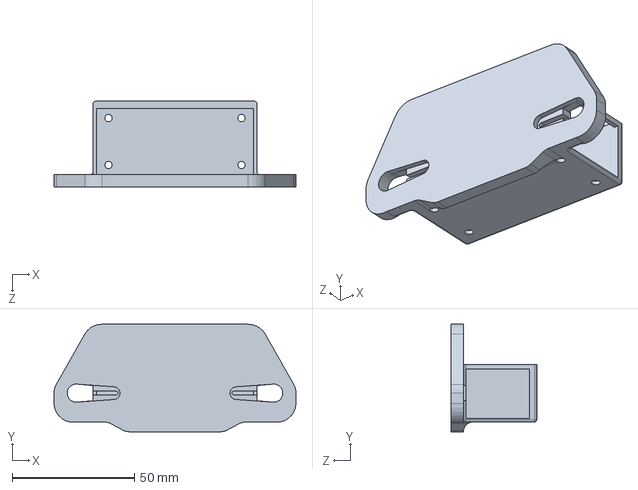
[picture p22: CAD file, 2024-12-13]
CAD/BackLeg_CAD/BackPartV2.SLDPRT
99.0 x 44.0 x 35.0 mm

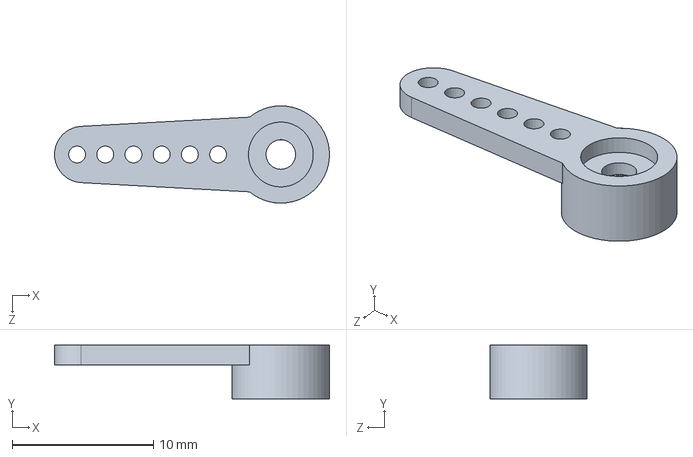
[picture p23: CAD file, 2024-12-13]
CAD/BodyComplete_CAD/SG90 - Micro Servo 9g - Tower Pro.2.SLDPRT
19.5 x 3.80 x 6.90 mm

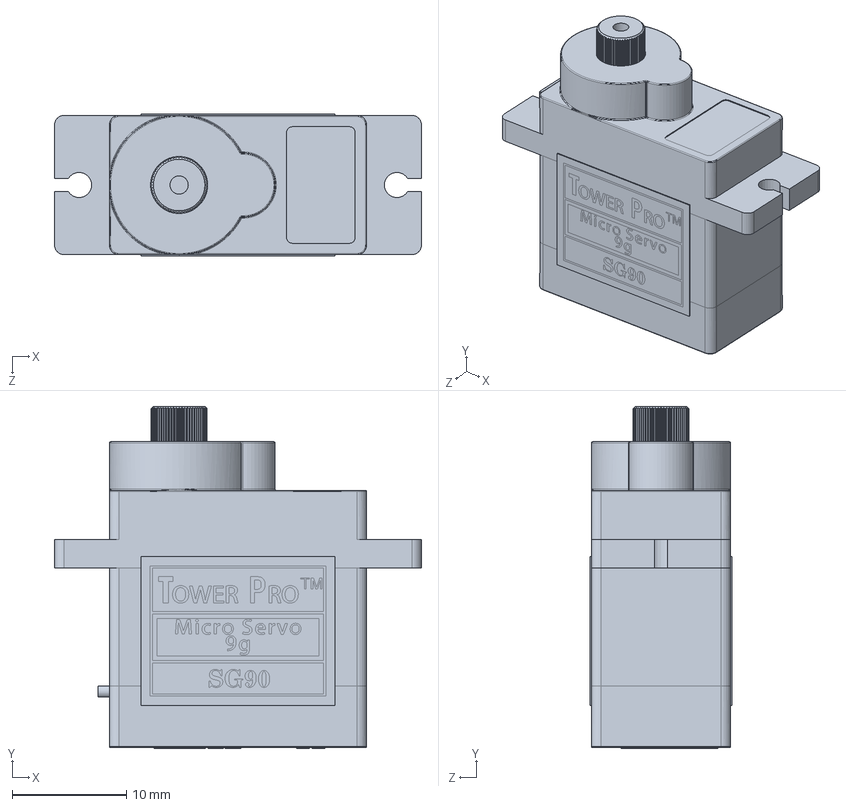
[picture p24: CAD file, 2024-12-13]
CAD/BodyComplete_CAD/SG90 - Micro Servo 9g - Tower Pro.1.SLDPRT
32.1 x 30.0 x 12.4 mm

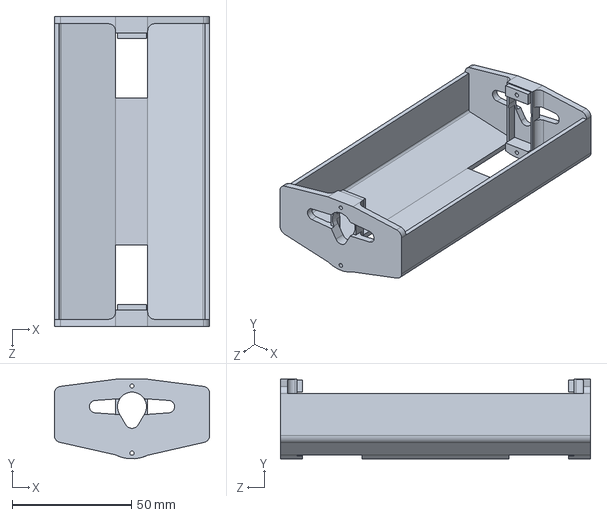
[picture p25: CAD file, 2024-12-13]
CAD/BodyComplete_CAD/Body.SLDPRT
65.2 x 33.3 x 130.0 mm

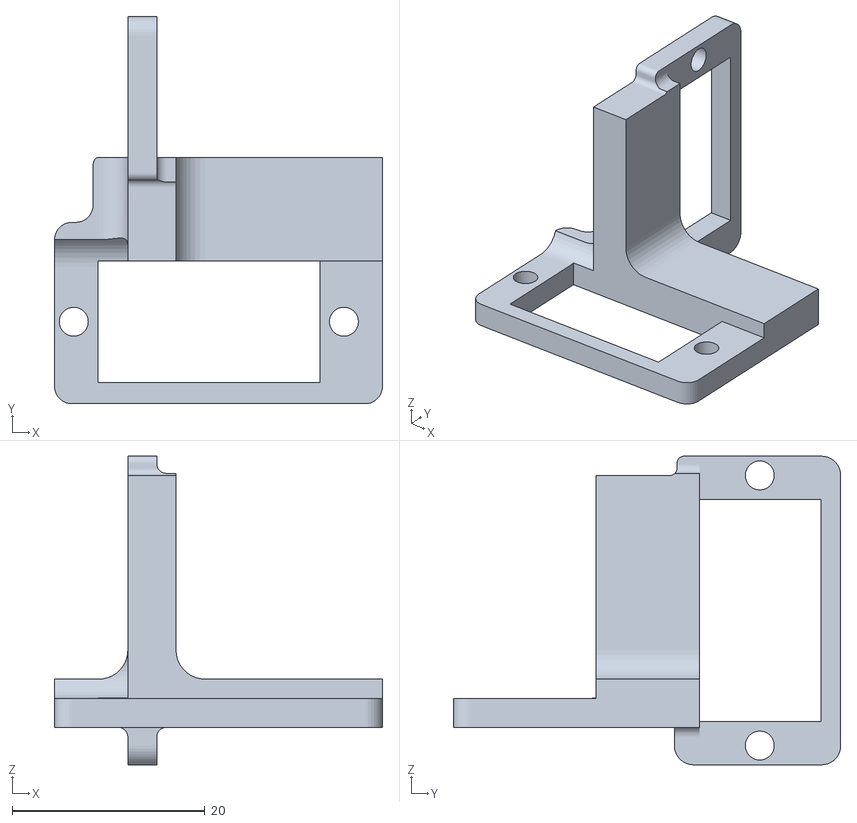
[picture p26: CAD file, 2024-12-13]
CAD/STL_Files/SoportePiezaV2.STL
34.0 x 40.2 x 32.0

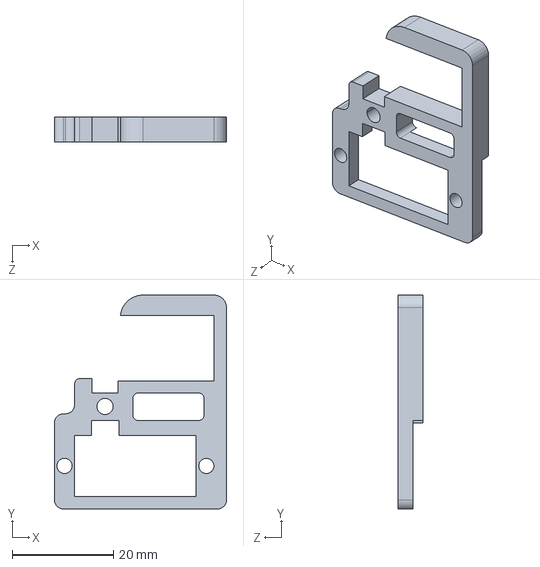
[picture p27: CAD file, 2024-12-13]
CAD/BackLeg_CAD/Piece1R.SLDPRT
34.0 x 42.2 x 5.00 mm

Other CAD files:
CAD/BackLeg_CAD/Piece1L.SLDASM
CAD/BackLeg_CAD/Piece2L.SLDASM
CAD/BodyComplete_CAD/Fermur_robot_V3.SLDPRT
CAD/STL_Files/BackPartV2.STL
CAD/STL_Files/Fermur_robot_V3.STL
CAD/BackLeg_CAD/Fermur_pata_V3.SLDPRT
CAD/BackLeg_CAD/SoportePiezaV2.SLDPRT
CAD/BodyComplete_CAD/BackPartV2.SLDPRT
CAD/BodyComplete_CAD/Fermur_pata_V3.SLDPRT
CAD/BodyComplete_CAD/SoportePiezaV2.SLDPRT

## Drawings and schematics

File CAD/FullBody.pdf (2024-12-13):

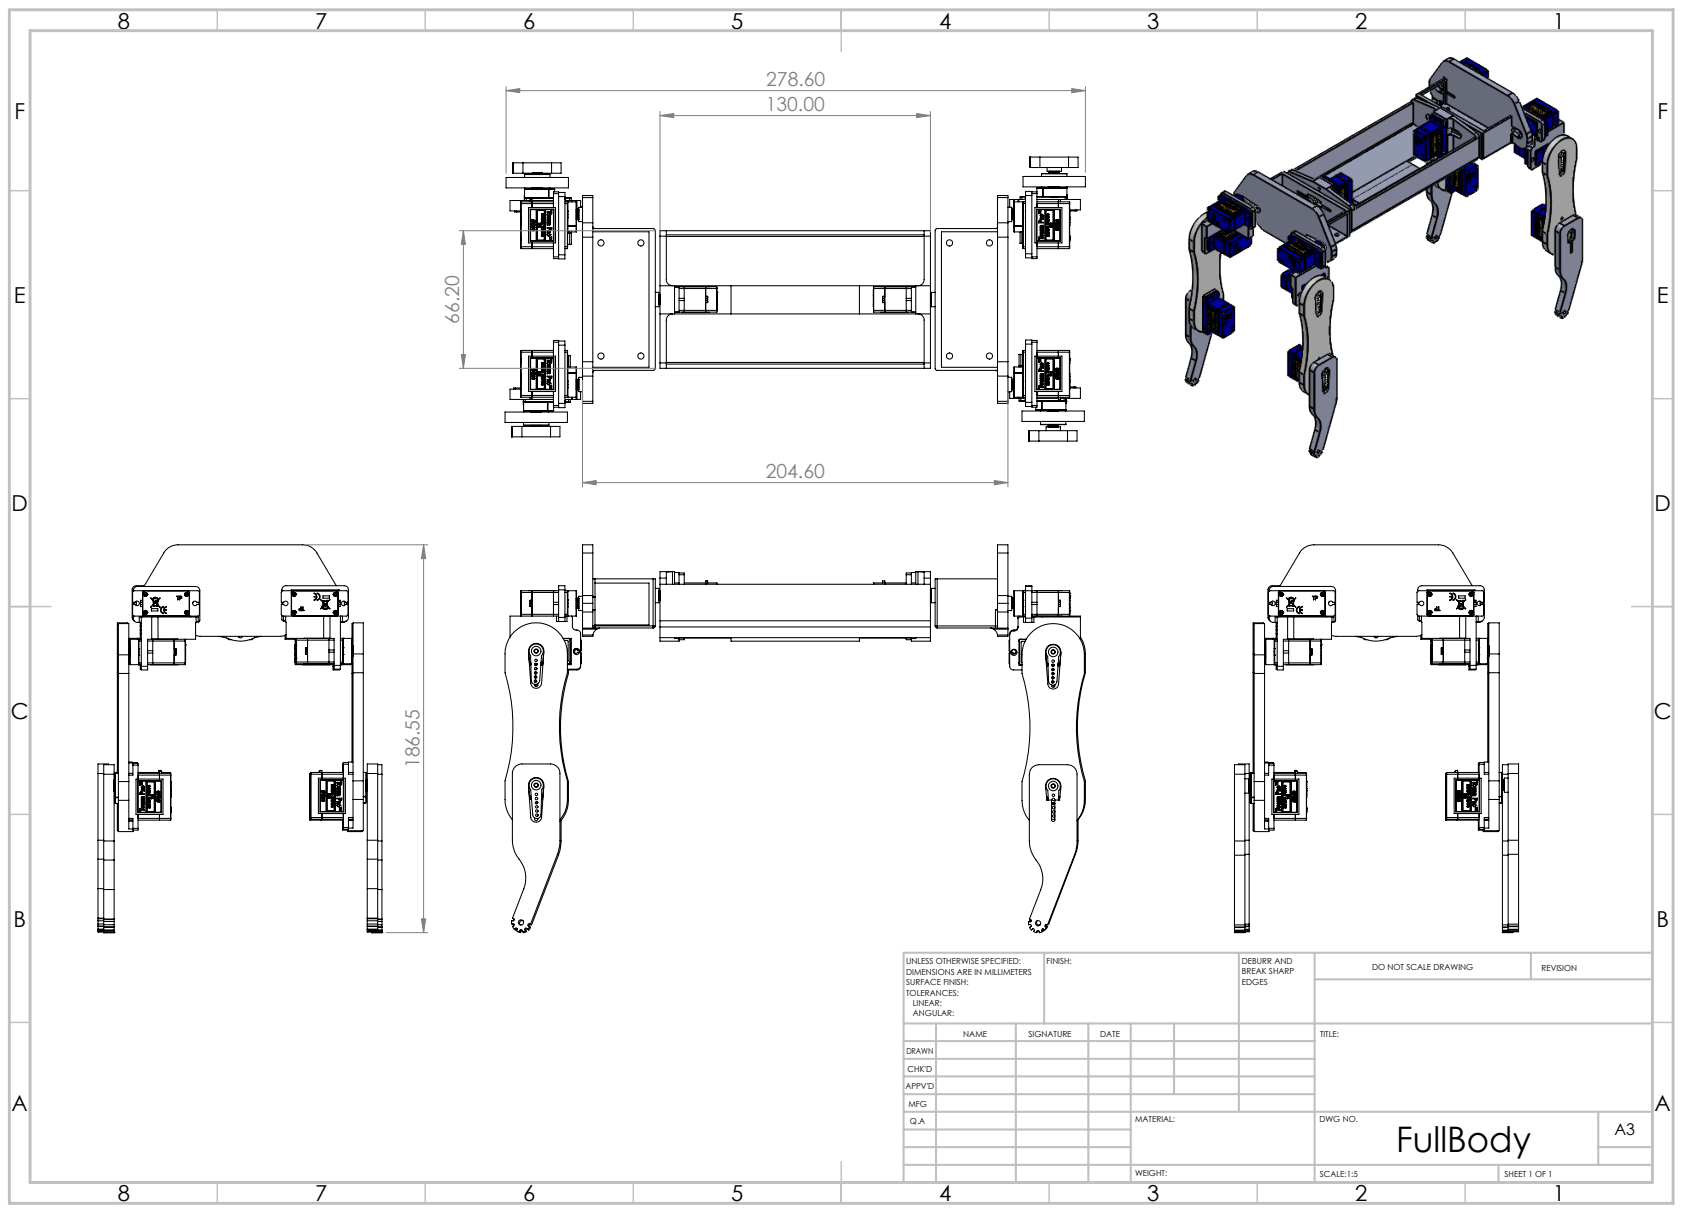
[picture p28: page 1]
FINISH:; DEBURR AND; BREAK SHARP; DO NOT SCALE DRAWING; REVISION; SCALE:1:5; SHEET 1 OF 1

UNLESS OTHERWISE SPECIFIED:
DIMENSIONS ARE IN MILLIMETERS
SURFACE FINISH:
TOLERANCES:
LINEAR:
ANGULAR:

NAME | SIGNATURE | DATE | | | | TITLE:

DRAWN
CHK'D
APPV'D
MFG
Q.A | | | | MATERIAL: | DWG NO. FullBody | A3

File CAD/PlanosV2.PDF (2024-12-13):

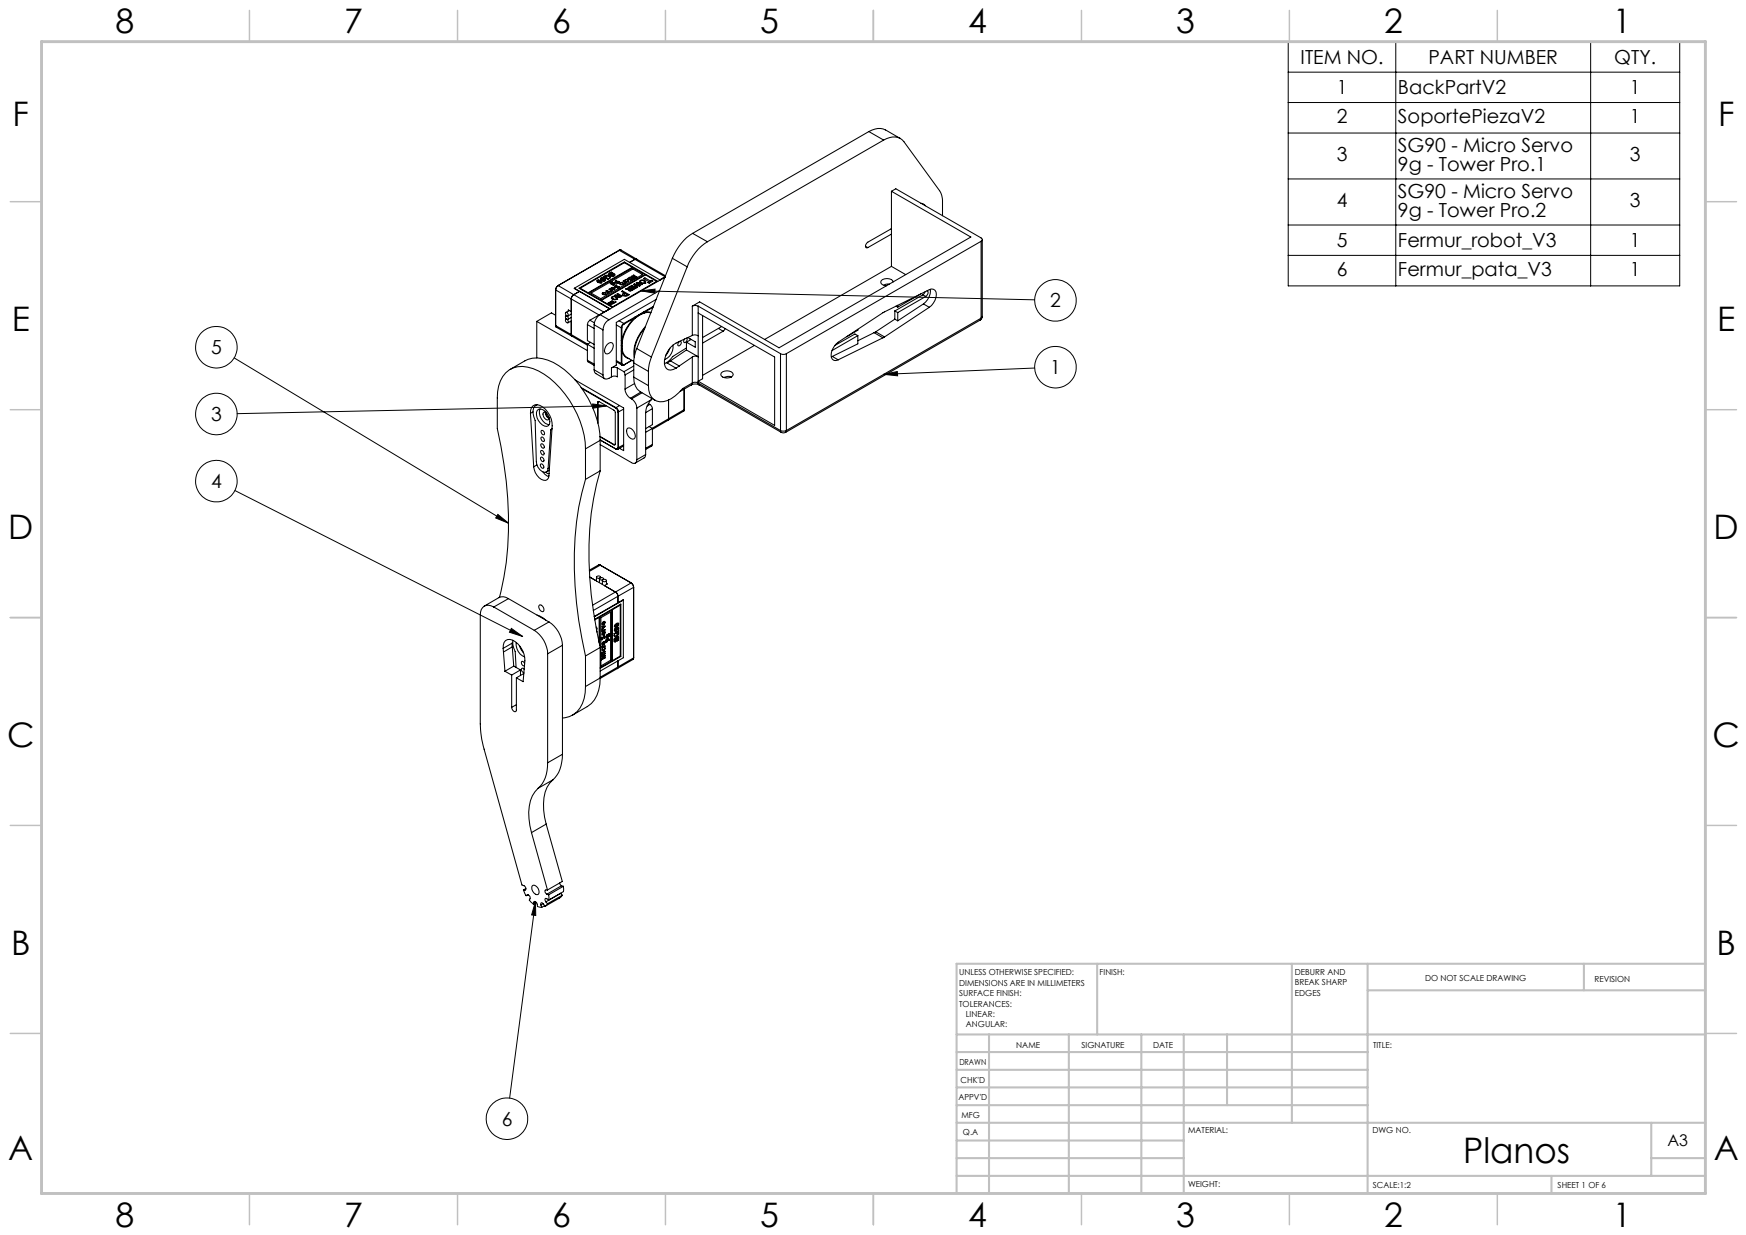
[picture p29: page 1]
FINISH:; DEBURR AND; BREAK SHARP; DO NOT SCALE DRAWING; REVISION; SCALE:1:2; SHEET 1 OF 6

ITEM NO. | PART NUMBER | QTY.
1 | BackPartV2 | 1
2 | SoportePiezaV2 | 1
3 | SG90 - Micro Servo 9g - Tower Pro.1 | 3
4 | SG90 - Micro Servo 9g - Tower Pro.2 | 3
5 | Fermur_robot_V3 | 1
6 | Fermur_pata_V3 | 1

UNLESS OTHERWISE SPECIFIED:
DIMENSIONS ARE IN MILLIMETERS
SURFACE FINISH:
TOLERANCES:
LINEAR:
ANGULAR:

NAME | SIGNATURE | DATE | | | | TITLE:

DRAWN
CHK'D
APPV'D
MFG
Q.A | | | | MATERIAL: | DWG NO. Planos | A3

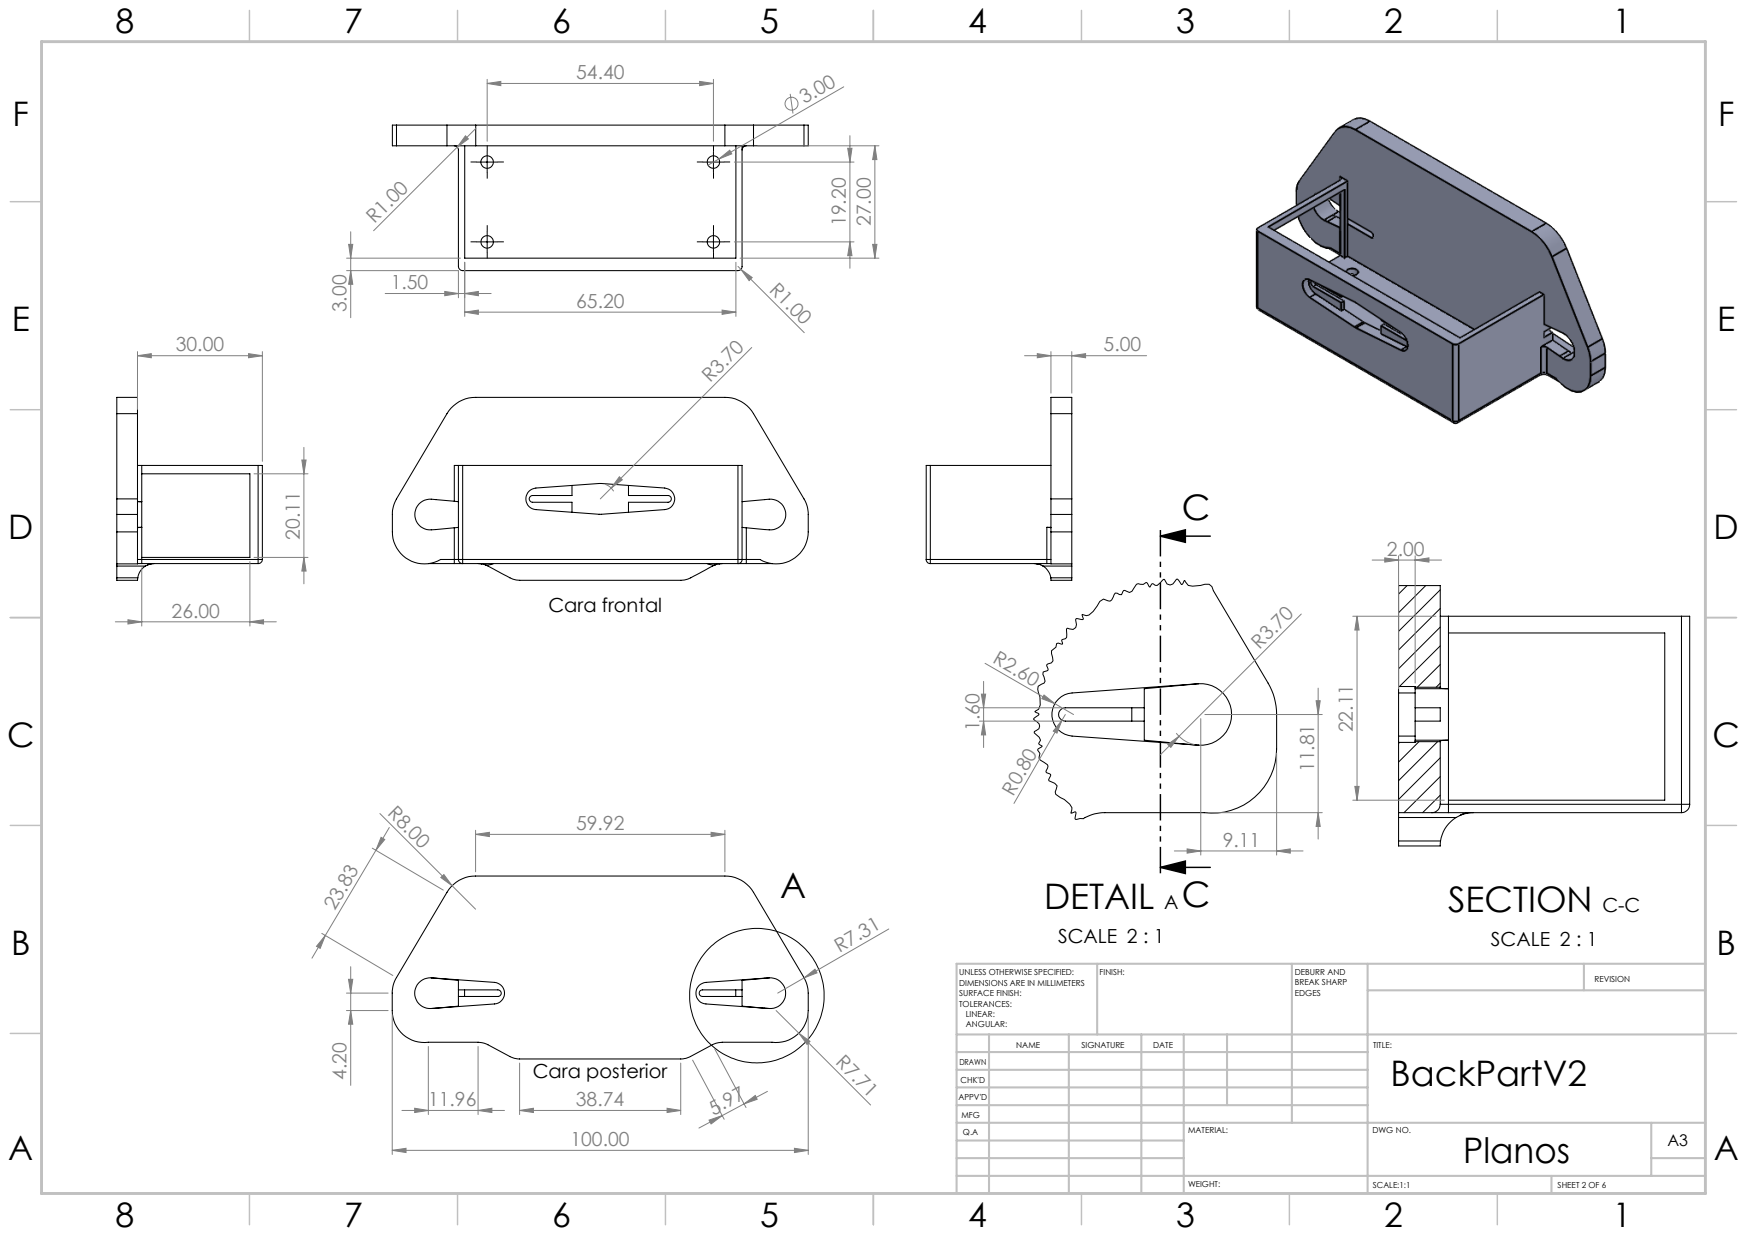
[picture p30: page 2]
Cara frontal; Cara posterior; DETAIL AC; SCALE 2 : 1; SECTION C-C; FINISH:; DEBURR AND; BREAK SHARP; SCALE:1:1; SHEET 2 OF 6

UNLESS OTHERWISE SPECIFIED:
DIMENSIONS ARE IN MILLIMETERS
SURFACE FINISH:
TOLERANCES:
LINEAR:
ANGULAR:

NAME | SIGNATURE | DATE | TITLE: BackPartV2

DRAWN
CHK'D
APPV'D
MFG

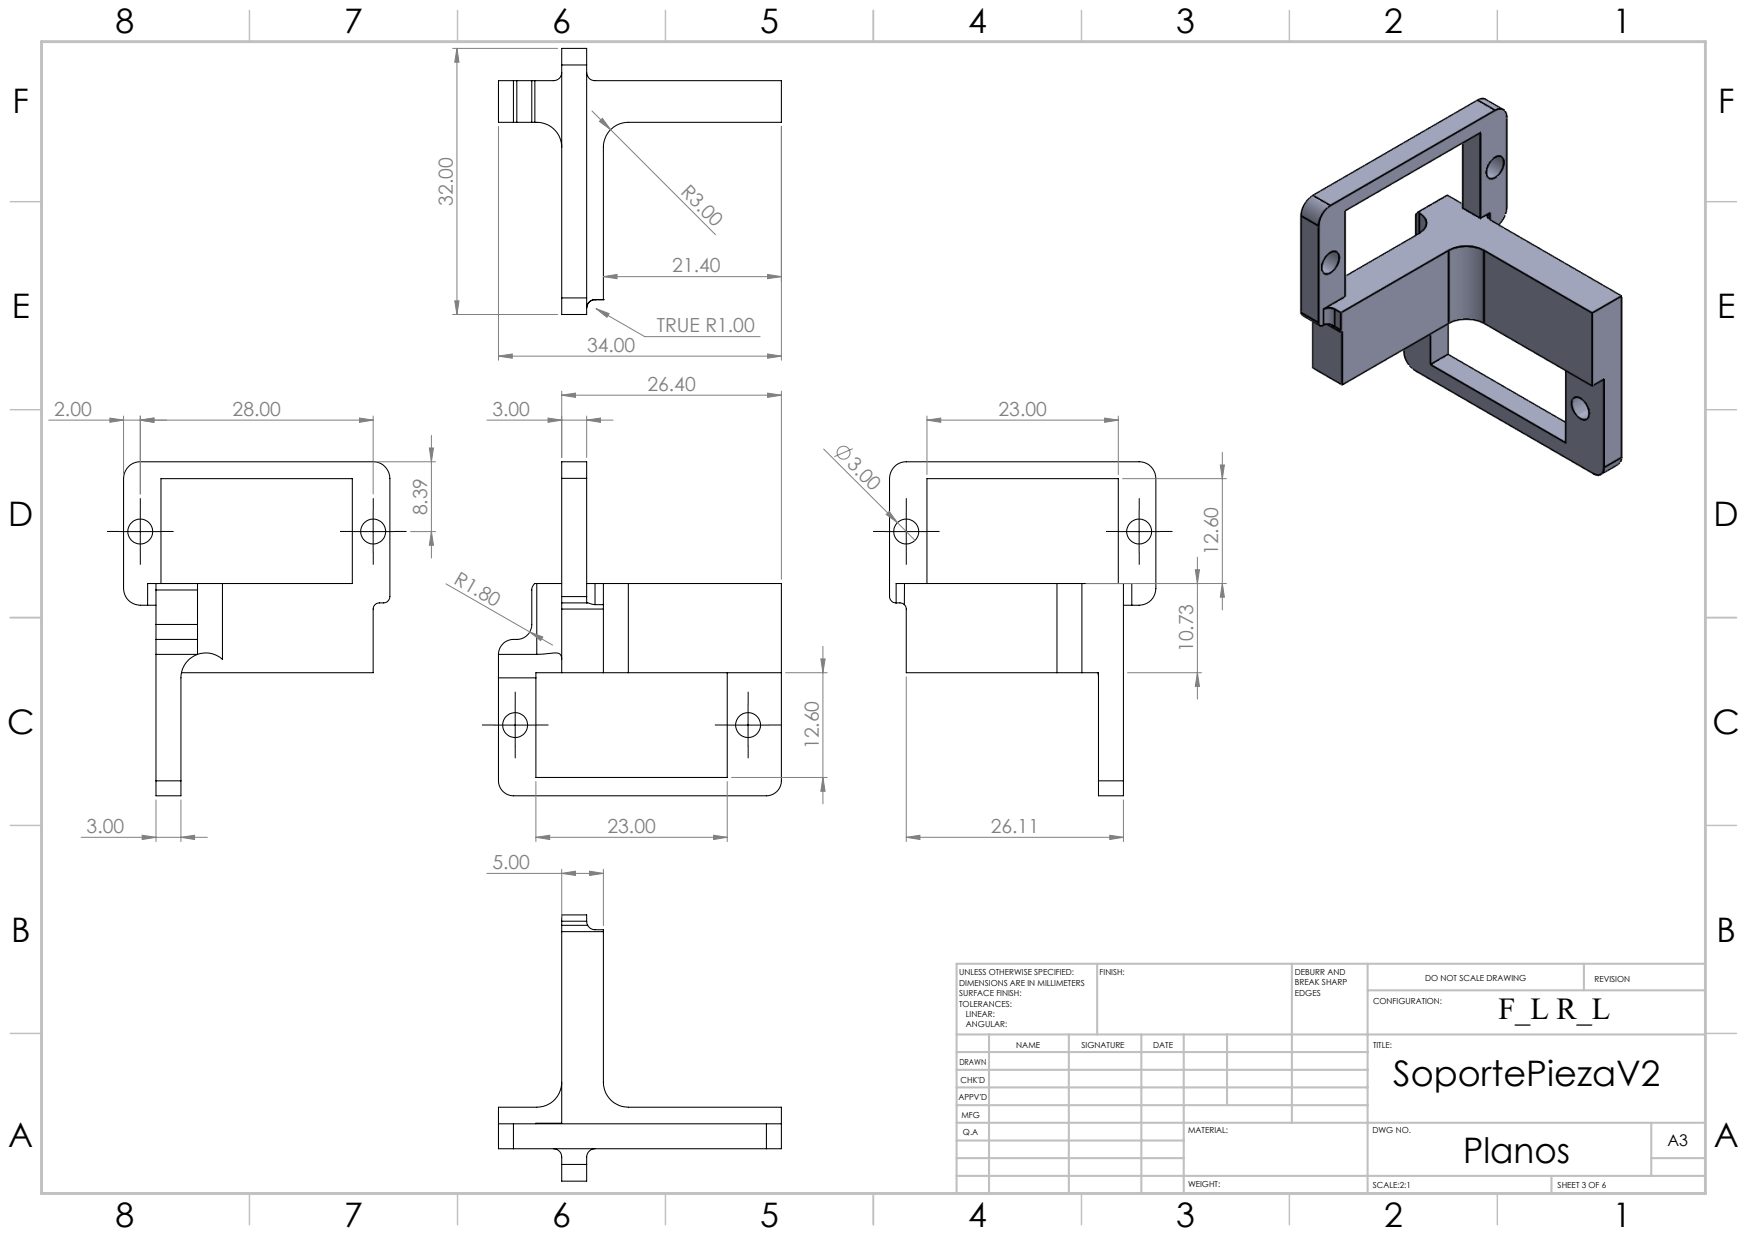
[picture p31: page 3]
TRUE R1.00; FINISH:; DEBURR AND; BREAK SHARP; DO NOT SCALE DRAWING; REVISION; SCALE:2:1; SHEET 3 OF 6

UNLESS OTHERWISE SPECIFIED:
DIMENSIONS ARE IN MILLIMETERS
SURFACE FINISH:
TOLERANCES:
LINEAR:
ANGULAR:

NAME | SIGNATURE | DATE | TITLE:
SoportePiezaV2 DRAWN

CHK'D
APPV'D
MFG

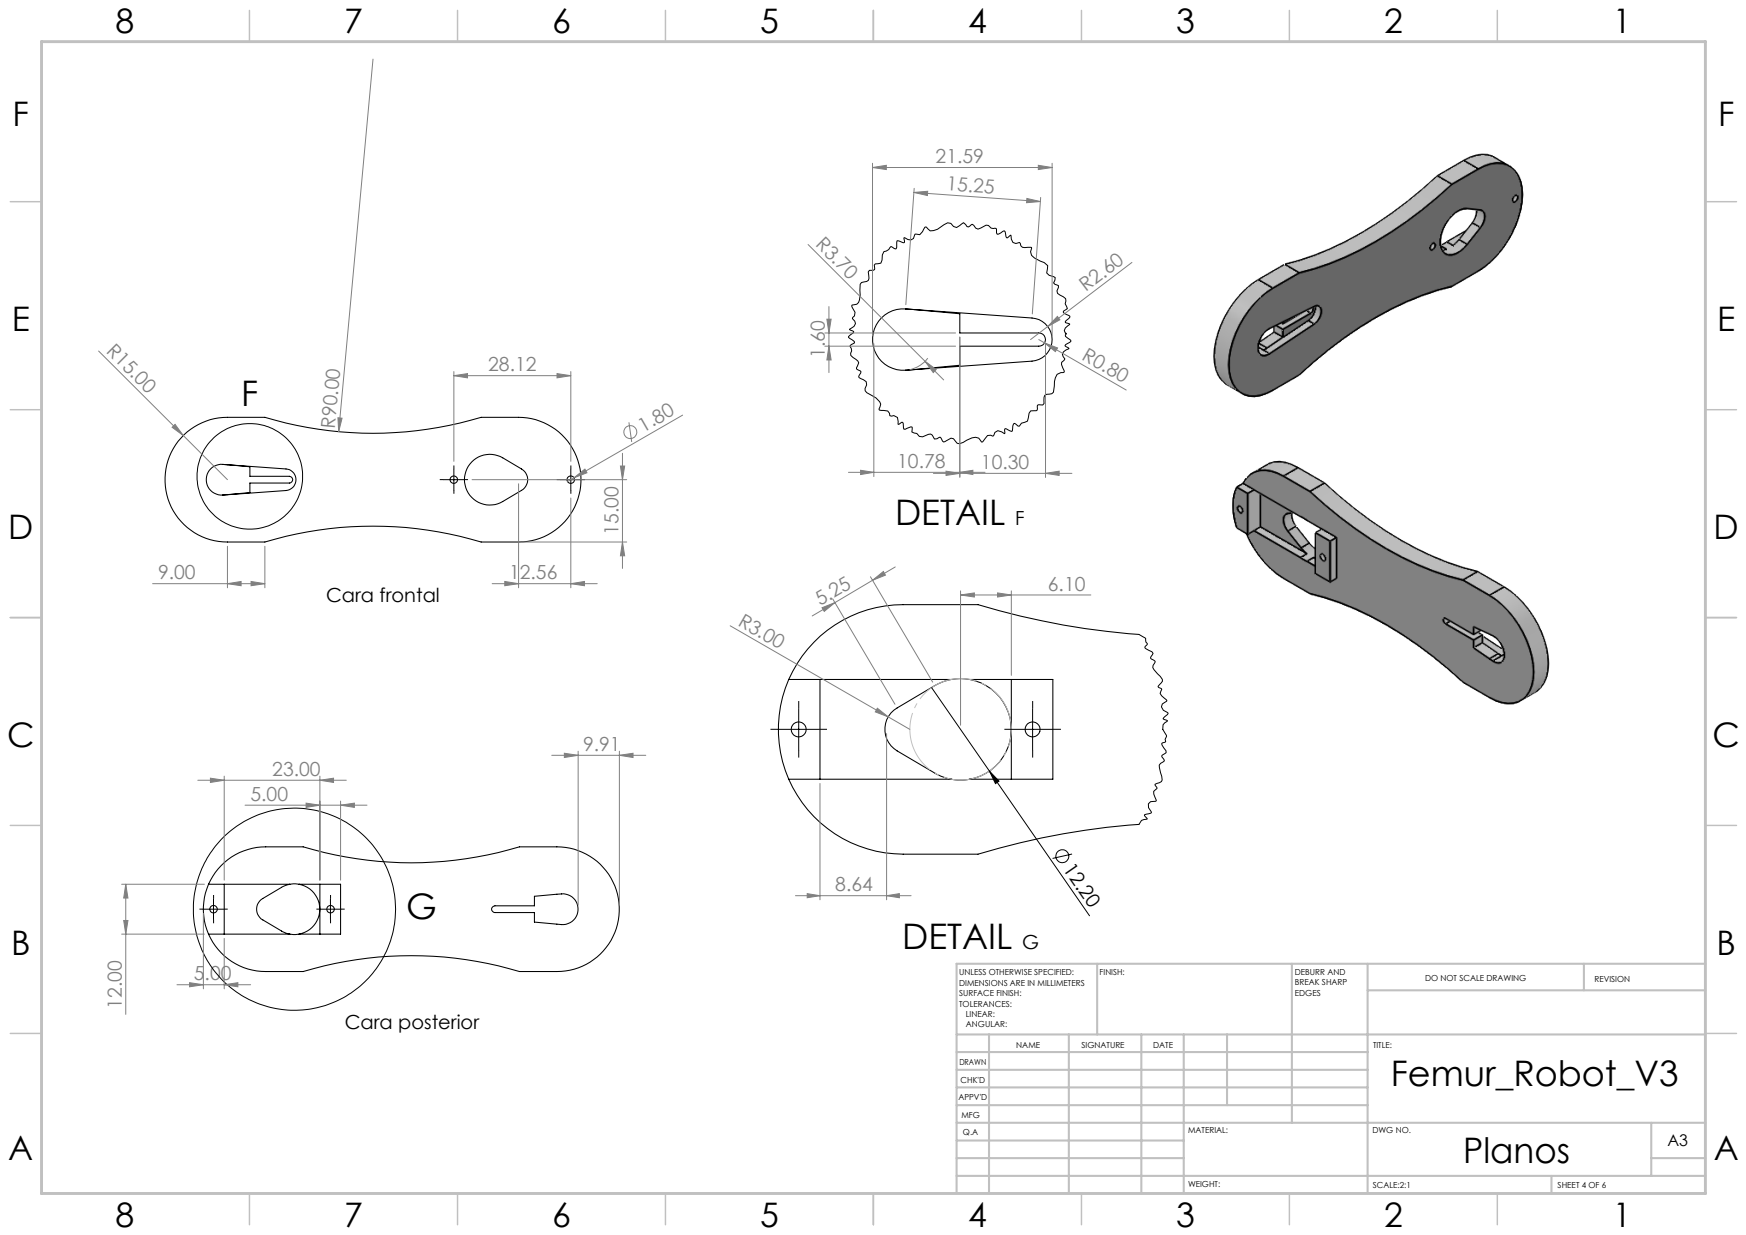
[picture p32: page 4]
Cara frontal; Cara posterior; DETAIL F; DETAIL G; FINISH:; DEBURR AND; BREAK SHARP; DO NOT SCALE DRAWING; REVISION

UNLESS OTHERWISE SPECIFIED:
DIMENSIONS ARE IN MILLIMETERS
SURFACE FINISH:
TOLERANCES:
LINEAR:
ANGULAR:

NAME | SIGNATURE | DATE | TITLE: Femur_Robot_V3

DRAWN
CHK'D
APPV'D
MFG

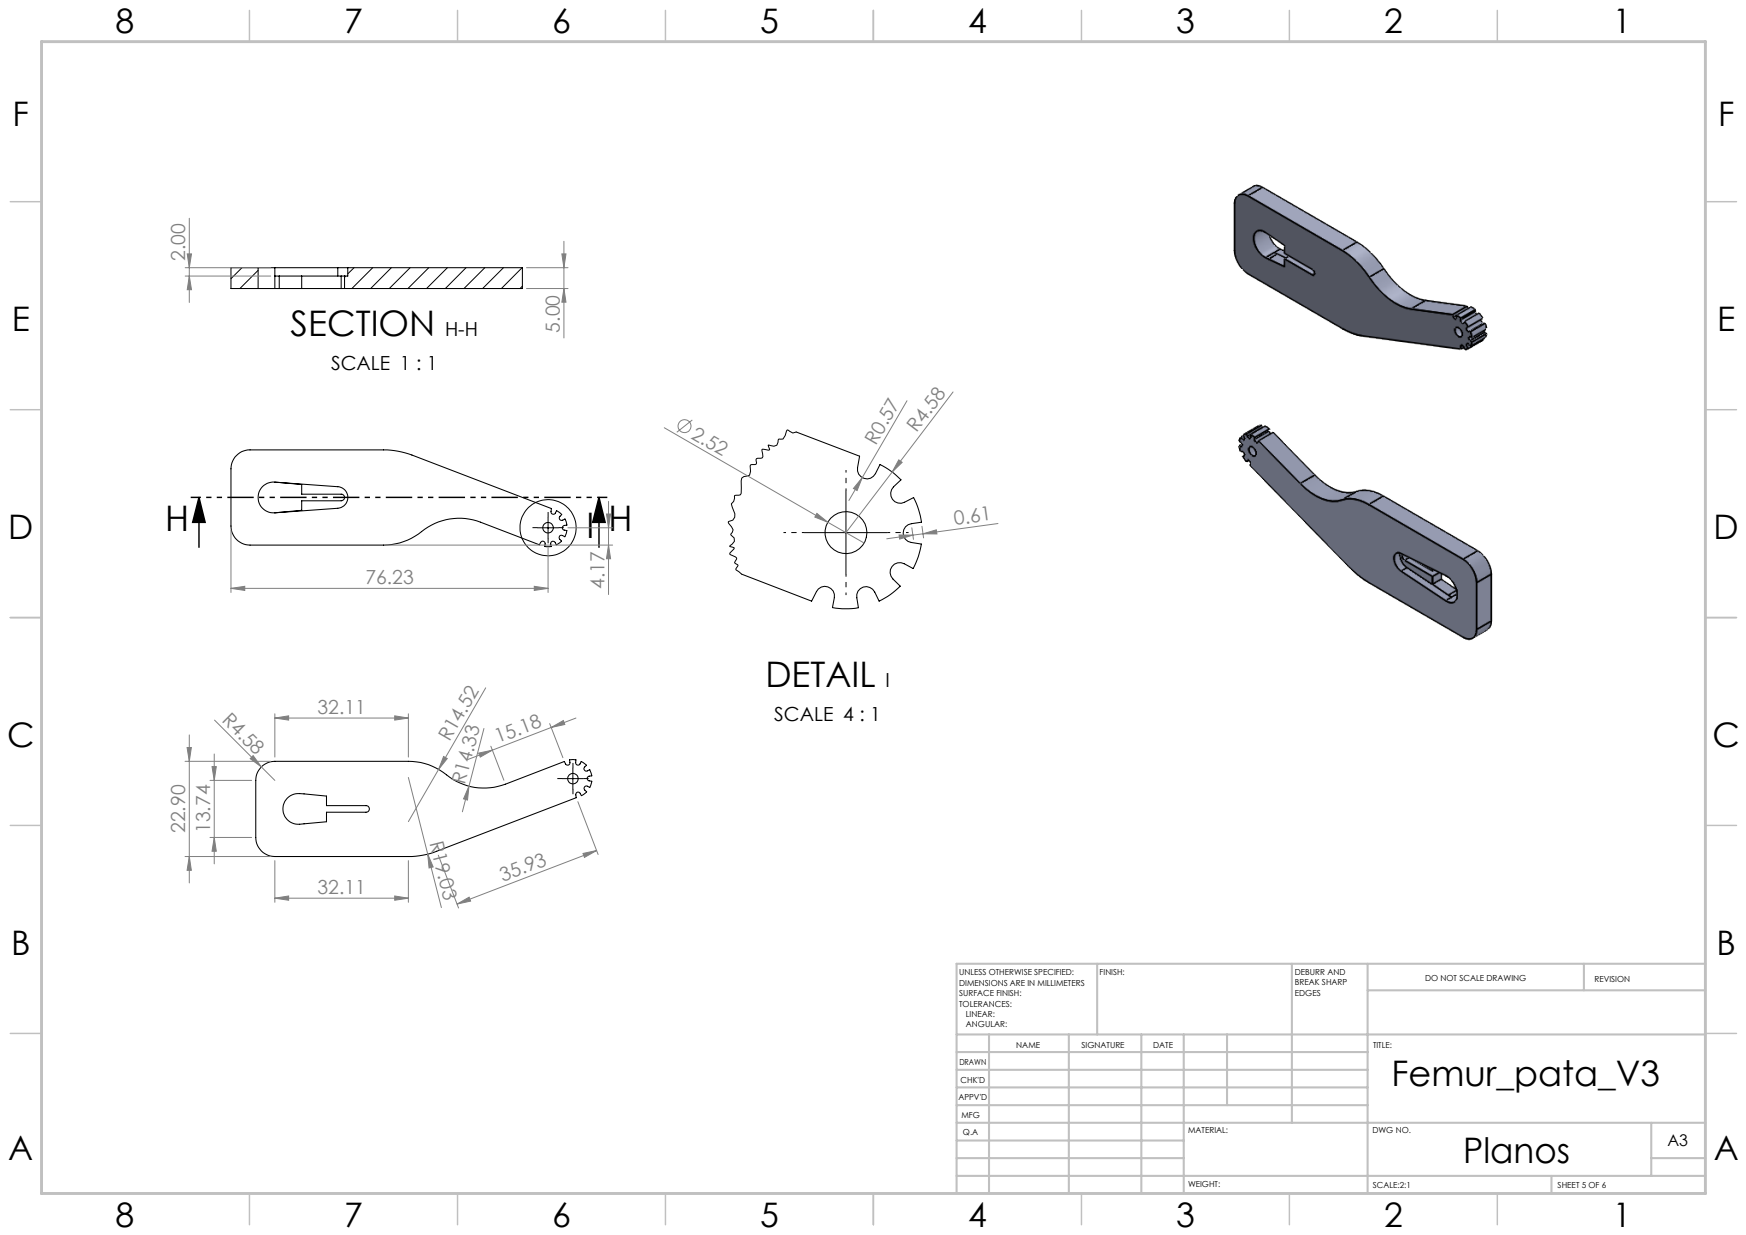
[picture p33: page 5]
SECTION H-H; SCALE 1 : 1; DETAIL I; SCALE 4 : 1; FINISH:; DEBURR AND; BREAK SHARP; DO NOT SCALE DRAWING; REVISION

UNLESS OTHERWISE SPECIFIED:
DIMENSIONS ARE IN MILLIMETERS
SURFACE FINISH:
TOLERANCES:
LINEAR:
ANGULAR:

NAME | SIGNATURE | DATE | TITLE: Femur_pata_V3

DRAWN
CHK'D
APPV'D
MFG

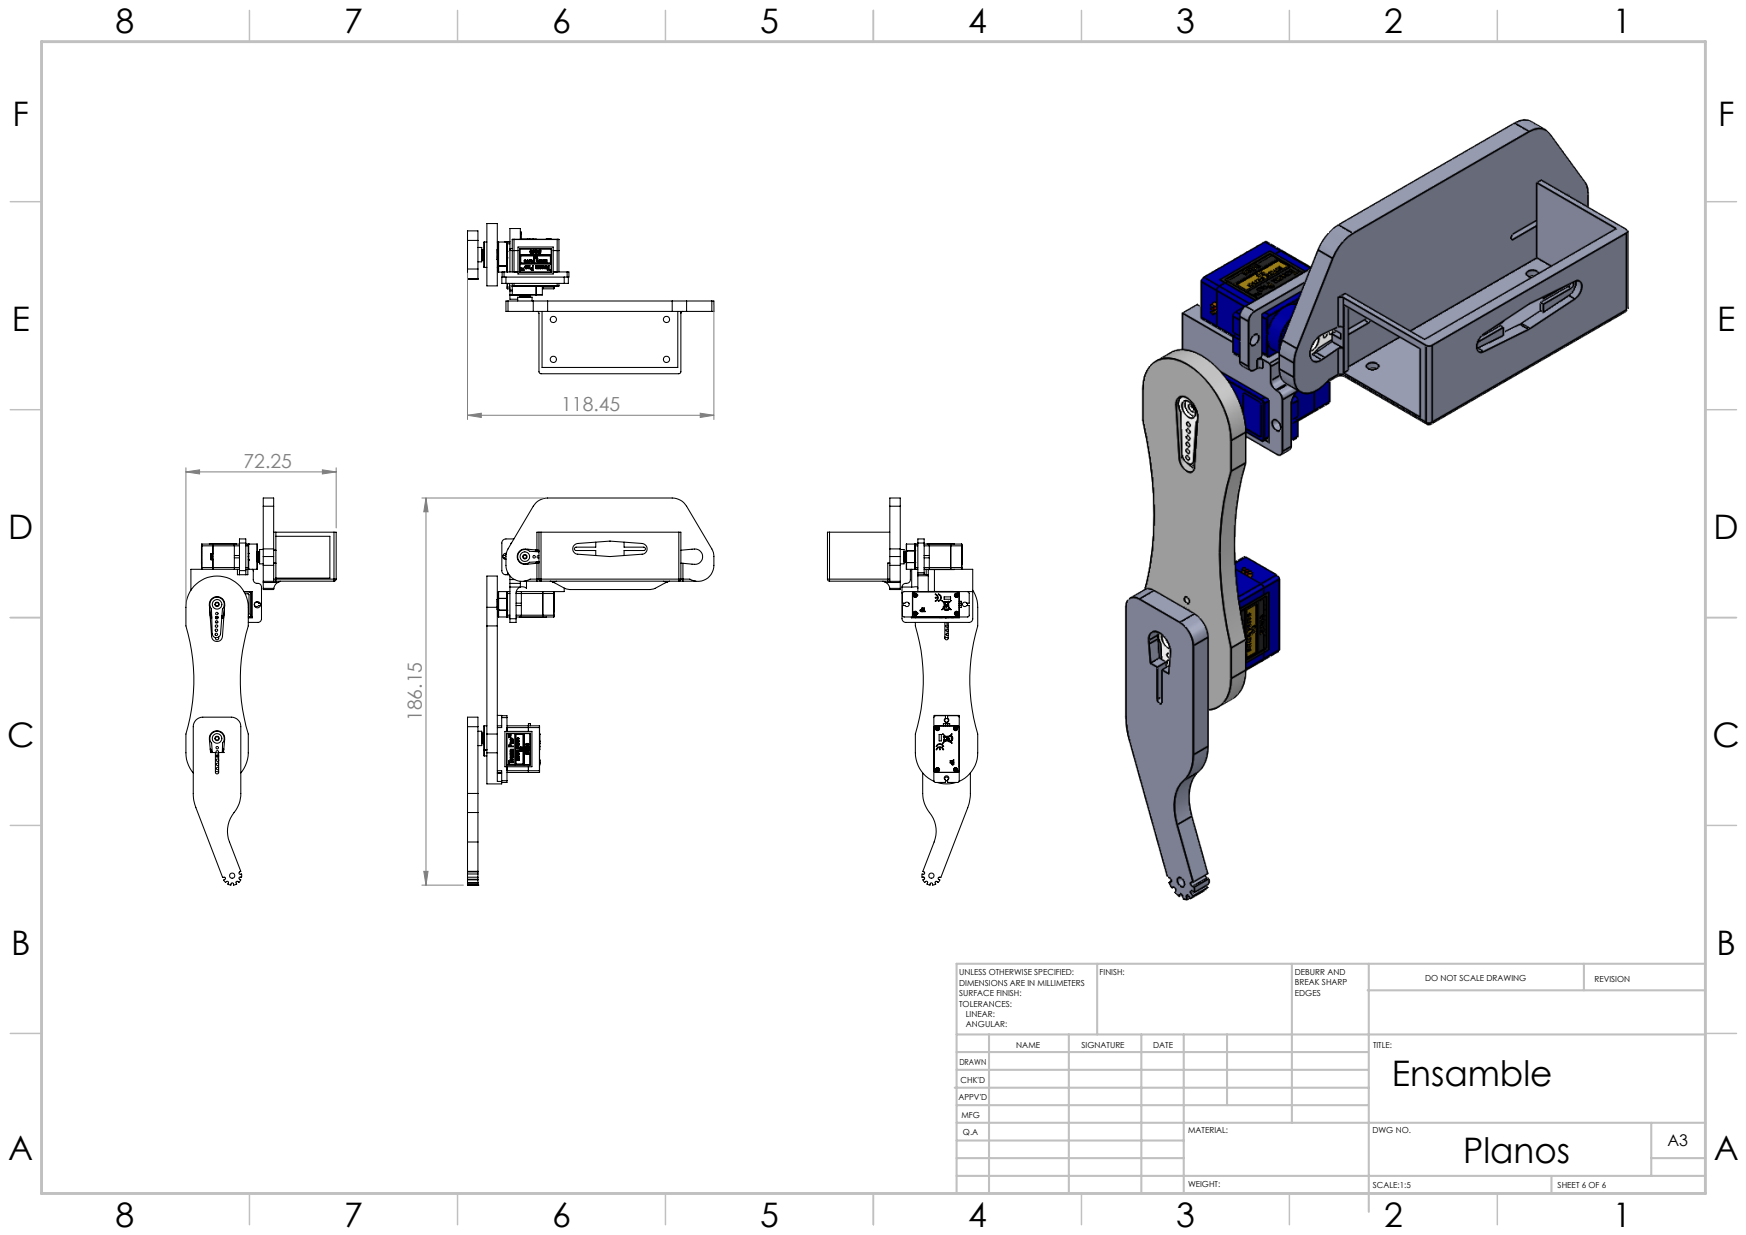
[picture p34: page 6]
FINISH:; DEBURR AND; BREAK SHARP; DO NOT SCALE DRAWING; REVISION; SCALE:1:5; SHEET 6 OF 6

UNLESS OTHERWISE SPECIFIED:
DIMENSIONS ARE IN MILLIMETERS
SURFACE FINISH:
TOLERANCES:
LINEAR:
ANGULAR:

NAME | SIGNATURE | DATE | TITLE: Ensamble

DRAWN
CHK'D
APPV'D
MFG

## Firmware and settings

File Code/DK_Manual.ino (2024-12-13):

#include <Servo.h>
#include <Math.h>

Servo servo1; // q1
Servo servo2; // q2 (fémur)
Servo servo3; // q3 (tibia)

const int servo1Pin = 9;
const int servo2Pin = 10;
const int servo3Pin = 11;

float q1_deg = 0.0;  // q1 = 0° modelo
float q2_deg = 0.0;  // Modelo: -90 a +90, 0 = 90° servo
float q3_deg = 0.0;  // Modelo: -90 a +90, 0 = 90° servo

void setup() {
  Serial.begin(9600);
  servo1.attach(servo1Pin);
  servo2.attach(servo2Pin);
  servo3.attach(servo3Pin);

  moveServos(q1_deg, q2_deg, q3_deg);

  float x, y, z;
  forwardKinematics(q1_deg, q2_deg, q3_deg, x, y, z);

  // Imprimir cabezales (opcional, se pueden omitir)
  Serial.println("x,y,z");
  // Imprimir posición inicial
  Serial.print(x); Serial.print(","); Serial.print(y); Serial.print(","); Serial.println(z);
  // Indicar al usuario cómo ingresar datos:
  Serial.println("Ingrese q2,q3 en [-90,90], ejemplo: 0,0");
}

void loop() {
  if (Serial.available() > 0) {
    String input = Serial.readStringUntil('\n');
    input.trim();
    int commaIndex = input.indexOf(',');

    if (commaIndex > 0) {
      String q2String = input.substring(0, commaIndex);
      String q3String = input.substring(commaIndex + 1);

      float q2Input = q2String.toFloat();
      float q3Input = q3String.toFloat();

      if (q2Input >= -90 && q2Input <= 90 && q3Input >= -90 && q3Input <= 90) {
        q2_deg = q2Input;
        q3_deg = q3Input;

        moveServos(q1_deg, q2_deg, q3_deg);

        float x, y, z;
        forwardKinematics(q1_deg, q2_deg, q3_deg, x, y, z);
        // Imprimir sólo valores x,y,z
        Serial.print(x); Serial.print(","); Serial.print(y); Serial.print(","); Serial.println(z);
      } else {
        Serial.println("Error: Angulos fuera de rango");
      }
    } else {
      Serial.println("Error: Formato incorrecto. Use q2,q3 (ej: 0,0)");
    }
  }
}

void forwardKinematics(float q1_deg, float q2_deg, float q3_deg, float &x, float &y, float &z) {
  float q1 = radians(q1_deg);
  float q2 = radians(q2_deg);
  float q3 = radians(q3_deg);

  float s1 = sin(q1);
  float c1 = cos(q1);
  float s2 = sin(q2);
  float c2 = cos(q2);
  float s23 = sin(q2 - q3);
  float c23 = cos(q2 - q3);

  x = 7.96*s1*s23 + 64.49*s1*c2 + 70.54*s1*c23 + 22.93*s1 + 25.06*c1;
  y = 25.06*s1 - 7.96*s23*c1 - 64.49*c1*c2 - 70.54*c1*c23 - 22.93*c1;
  z = -64.49*s2 - 70.54*s23 + 7.96*c23 + 24.25;
}

void moveServos(float q1_model, float q2_model, float q3_model) {
  // Mapear q2 y q3 al servo
  float servo2_angle = q2_model + 90.0;     // q2: 0° modelo→90° servo, +90° modelo→180°, -90°→0°
  float servo3_angle = 90.0 - q3_model;     // q3: 0° modelo→90° servo, +90°→0°, -90°→180°
  float servo1_angle = q1_model;            // q1 sin ajuste

  servo1_angle = constrain(servo1_angle, 0, 180);
  servo2_angle = constrain(servo2_angle, 0, 180);
  servo3_angle = constrain(servo3_angle, 0, 180);

  servo1.write(servo1_angle);
  servo2.write(servo2_angle);
  servo3.write(servo3_angle);
}

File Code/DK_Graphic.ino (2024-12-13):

#include <Servo.h>
#include <Math.h>

// Definir Servos
Servo servo1; 
Servo servo2; 
Servo servo3; 

const int servo1Pin = 9;
const int servo2Pin = 10;
const int servo3Pin = 11;

float q1_deg = 0.0;  // q1 fijo en 0° para este ejemplo

// forwardKinematics: Calcula x,y,z dados q1_deg, q2_deg, q3_deg (en grados)
void forwardKinematics(float q1_deg, float q2_deg, float q3_deg, float &x, float &y, float &z) {
  float q1 = radians(q1_deg);
  float q2 = radians(q2_deg);
  float q3 = radians(q3_deg);

  float s1 = sin(q1);
  float c1 = cos(q1);
  float s2 = sin(q2);
  float c2 = cos(q2);
  float s23 = sin(q2 - q3);
  float c23 = cos(q2 - q3);

  x = 7.96*s1*s23 + 64.49*s1*c2 + 70.54*s1*c23 + 22.93*s1 + 25.06*c1;
  y = 25.06*s1 - 7.96*s23*c1 - 64.49*c1*c2 - 70.54*c1*c23 - 22.93*c1;
  z = -64.49*s2 - 70.54*s23 + 7.96*c23 + 24.25;
}

// moveServos: Ajusta servos según q2, q3 en el modelo
void moveServos(float q1_model, float q2_model, float q3_model) {
  float servo1_angle = q1_model;
  float servo2_angle = q2_model + 90.0;    
  float servo3_angle = 90.0 - q3_model;

  servo1_angle = constrain(servo1_angle, 0, 180);
  servo2_angle = constrain(servo2_angle, 0, 180);
  servo3_angle = constrain(servo3_angle, 0, 180);

  servo1.write(servo1_angle);
  servo2.write(servo2_angle);
  servo3.write(servo3_angle);
}

// Secuencia con incrementos de 45°
float sequence[][3] = {
    {0, -90, 90},
    {0, -90, 45},
    {0, -90, 0},
    {0, -90, -45},
    {0, -90, -90},
    {0, -45, 90},
    {0, -45, 45},
    {0, -45, 0},
    {0, -45, -45},
    {0, -45, -90},
    {0, 0, 90},
    {0, 0, 45},
    {0, 0, 0},
    {0, 0, -45},
    {0, 0, -90},
    {0, 45, 90},
    {0, 45, 45},
    {0, 45, 0},
    {0, 45, -45},
    {0, 45, -90},
    {0, 90, 90},
    {0, 90, 45},
    {0, 90, 0},
    {0, 90, -45},
    {0, 90, -90}
};

int num_steps = sizeof(sequence)/sizeof(sequence[0]);

void setup() {
  Serial.begin(9600);
  servo1.attach(servo1Pin);
  servo2.attach(servo2Pin);
  servo3.attach(servo3Pin);

  Serial.println("x,y,z"); // Encabezado opcional

  // Posición inicial
  float x, y, z;
  q1_deg = 0; // q1 fijo, en este caso
  float q2_deg = sequence[0][1];
  float q3_deg = sequence[0][2];
  moveServos(q1_deg, q2_deg, q3_deg);
  forwardKinematics(q1_deg, q2_deg, q3_deg, x, y, z);
  Serial.print(x); Serial.print(","); Serial.print(y); Serial.print(","); Serial.println(z);
}

void loop() {
  // Iterar sobre la secuencia
  for (int i = 0; i < num_steps; i++) {
    float q1_deg = sequence[i][0];
    float q2_deg = sequence[i][1];
    float q3_deg = sequence[i][2];

    // Mover servos a la posición
    moveServos(q1_deg, q2_deg, q3_deg);

    // Calcular cinemática directa
    float x, y, z;
    forwardKinematics(q1_deg, q2_deg, q3_deg, x, y, z);

    // Imprimir x,y,z
    Serial.print(x); Serial.print(","); Serial.print(y); Serial.print(","); Serial.println(z);

    delay(1000); // Esperar 1s entre cada posición para que se vea el cambio en el plot
  }

}

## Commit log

2024-12-13 code and cad files
    [BackPartV2.SLDPRT, BackPartV2.STL, Body.SLDPRT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]
2024-12-13 Removed unused CAD files and STL files
    [Femur top.STL, Fermur_pata.SLDPRT, Fermur_pata.STL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]
